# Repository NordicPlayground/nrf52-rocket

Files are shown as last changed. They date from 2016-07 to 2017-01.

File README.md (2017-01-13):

# nRF52 Rocket

# Check out the official [Launch Video](https://www.youtube.com/watch?v=nOK4TQ3TGd8) from Nordic Semiconductor!

#### Table of Contents
* [Introduction](#introduction)
* [Hardware](#hardware)
* [Firmware](#firmware)

This repository contains the firmware and hardware files for the first launched BLE rocket prototype.

## Introduction

As the BLE standard (namely Bluetooth 5.0) enables higher TX power and thusly communication range, it becomes more and more viable to use Bluetooth LE for mid-range RC toys in the proximity of around 100 - 500 m. BLE provides the benefits of high interoperability amongst different manufacturers due to rigorous standardization compared to other frequencies, yet less power consuming than Wifi.

The model rocketry industry drives a very popular hobby, especially in the U.S., that inspires youth and adults to engage in science and engineering. Yet, through some web research it appears that there is a gap between really simple beginner rockets with less than 200 m of flight range which are completely made out of cardboard and wood with no electronic flight telemetry or electronic parachute deployment; and the advanced heavy duty rockets with expensive electronics that can go up to kilometers.

A BLE enabled model rocket can serve the hobbyists who want to be a little more serious with their rocket flying and track their rockets performance in real time and have smart parachute deployment, but do not have the funds or the skills to buy/build a super hardcore rocket that costs thousands of dollars.

## Hardware

### Rocket:
#### Electronics
Componenet Type | Part Number | Function
---:|---:|---:|
Processor/RF| nRF52 | Flight Control, launch control, telemetry, communication with ground station
Radio Amplifier (PA + LNA)| Skyworks 66112-11 | Boost RF range
IMU | MPU9250 | Orientation tracking, parachute deployment upon flight peak
Pressure | MPL3115A2 | Altitude tracking based on atmospheric pressure, parachute release timing upon flight peak
Humidity/Temperature | HTU21D | Environment monitoring
Servo Motors | Tower Pro SG90 | Parachute release mechanism
5V Boost Converter  | MIC2875 | Ignition and servo power
3F Supercapacitor | PM-5R0H305-R | High current ignition reservoir
3.3V LDO | AP7333-33SAG-7 | nRF52/sensor power
USB 4.2V LiPo Charger | AAT3681A | Charging

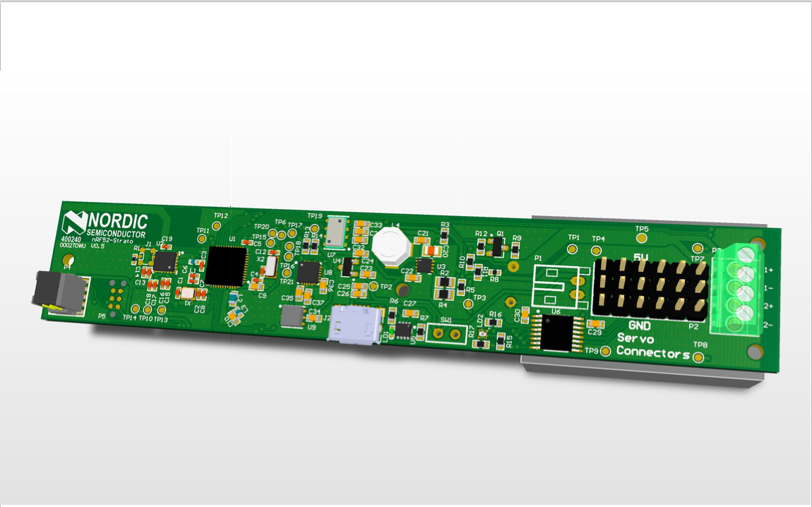
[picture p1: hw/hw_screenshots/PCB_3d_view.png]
3D View

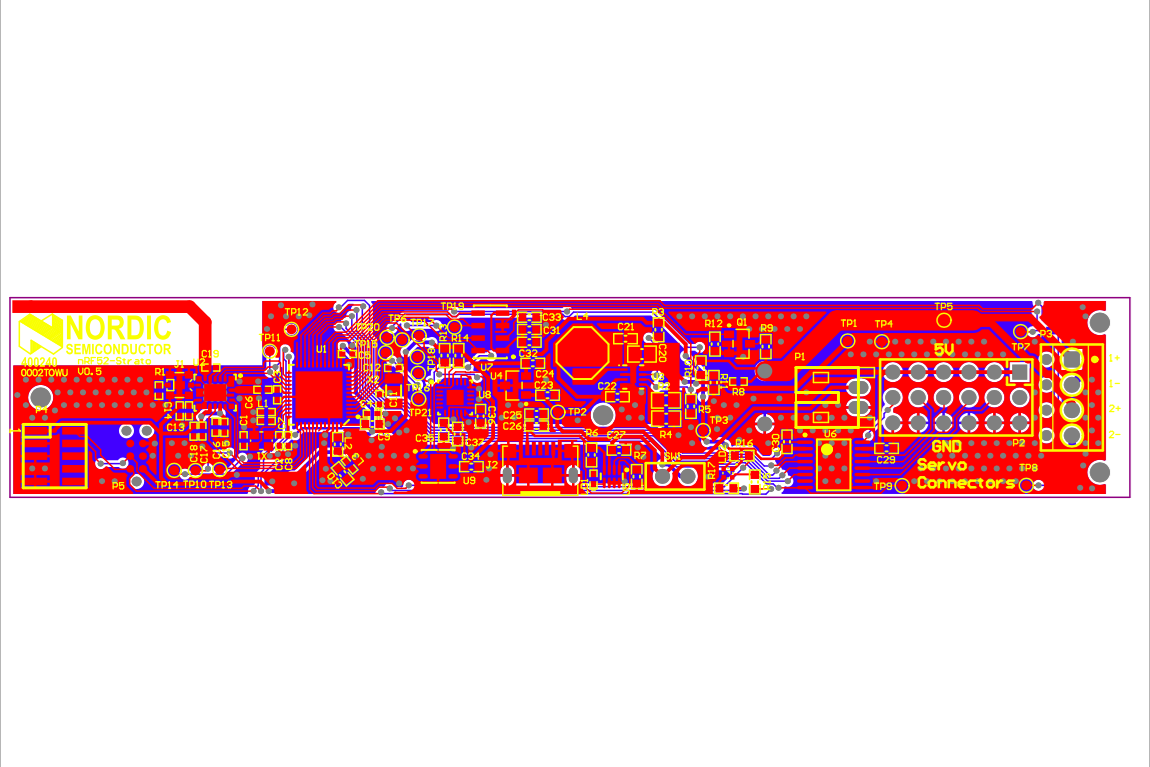
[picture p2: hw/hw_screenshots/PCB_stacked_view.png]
Stacked View


#### Mechanical
Component Type | Part Number | Function
---:|---:|---:|
Rocket Motor| Klima D9-P | Propulsion
Electronic Starters | Klima | Ignition mechanism
Parachute | Klima | Rocket recovery
Nose Cone | 3D Printed | Body construction
Engine Mount + Fins | 3D Printed | Body construction

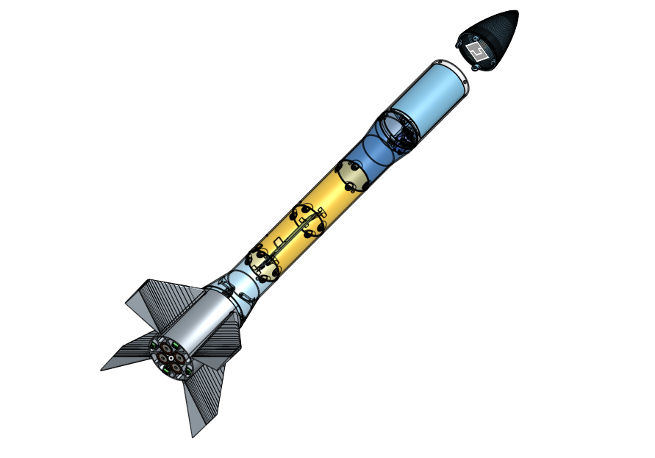
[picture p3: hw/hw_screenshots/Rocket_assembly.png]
Rocket CAD Assembly


[OnShape 3D CAD Files and Assemblies](https://cad.onshape.com/documents/a4d45ed022dbb8a2dc83f180/w/58fca6c234a131fe917f28c8/e/50b00e1e04cebf07ed807ff0 "Rocket CAD Files")

##Firmware

(Coming Soon!)

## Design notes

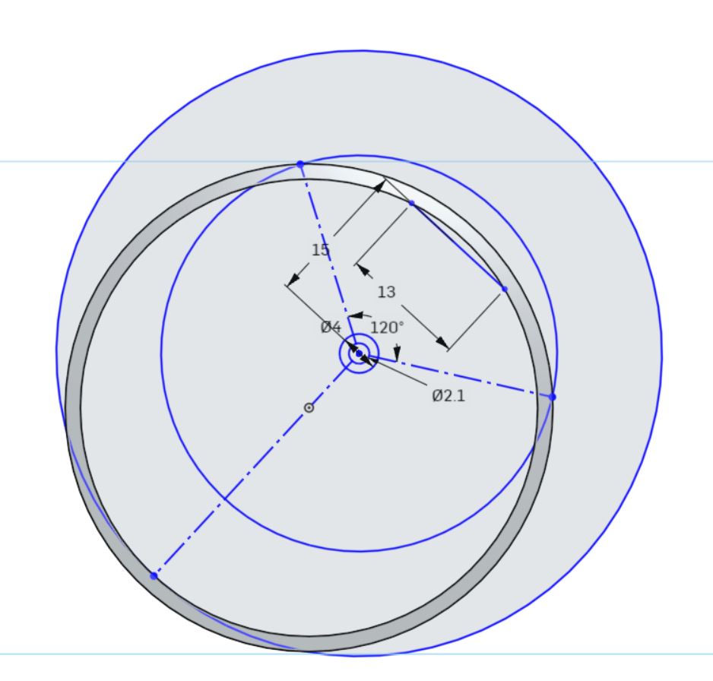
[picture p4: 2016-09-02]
hw/design process/parachute_hatch_sketch.JPG

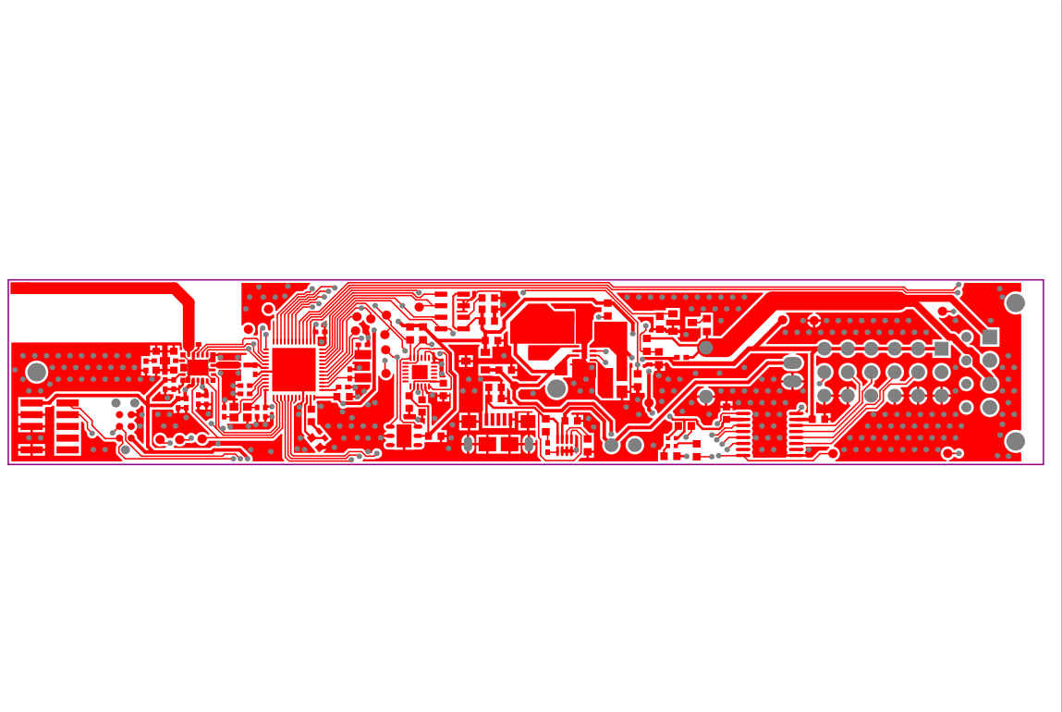
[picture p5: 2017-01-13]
hw/hw_screenshots/PCB_top_layer.png

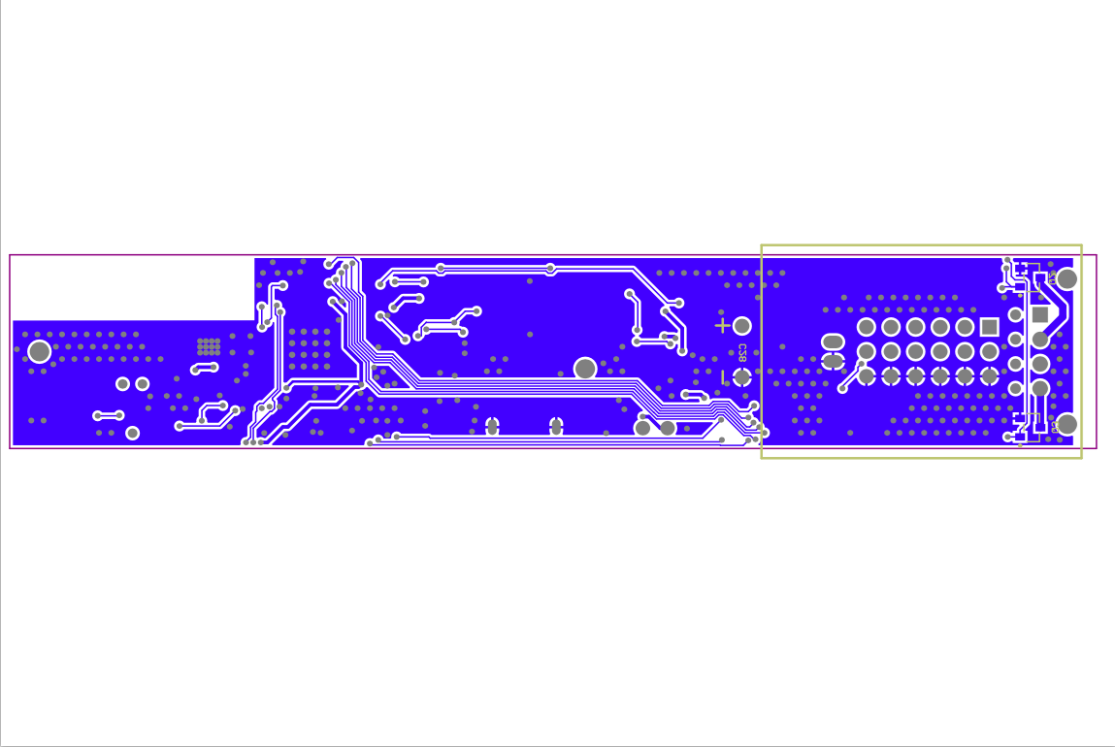
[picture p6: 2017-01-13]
hw/hw_screenshots/PCB_bottom_layer.png

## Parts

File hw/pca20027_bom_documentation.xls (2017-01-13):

Bill of material
PCB: | PCAxxxxx
Version: | <Schematic version>
Designator | Value | Description | Footprint Doc | Manufacturer | Manufacturer Part Number
C1, C2, C11, C12 | 12pF | Capacitor, NP0, ±2% | 0402
C3 | 0.8pF | Capacitor, NP0, ±5% | 0402
C4, C5, C8, C14, C16, C18, C19 | 100nF | Capacitor, X7R, ±10% | 0402
C6 | N.C. | Not mounted | 0402
C7 | 100pF | Capacitor, NP0, ±5% | 0402
C9, C21 | 4.7µF | Capacitor, X5R, ±10% | 0603
C10, C22, C23, C24 | 1.0µF | Capacitor, X7R, ±10% | 0603
C13, C15, C17 | 1.0nF | Capacitor, X7R, ±10% | 0402
C20 | 22µF | Capacitor, X5R, ±10% | 0805
C25, C27, C31 | 10µF | Capacitor, X5R, ±20% | 0603
C26, C29, C30, C32, C33, C34, C35, C37 | 100nF | Chip Cap 0603 | 0603
C28 | 3F | 3F, 5V Supercapacitor (EDLC) | PM-5R0H305-R | Cooper Industries | PM-5R0H305-R
C36 | 10nF | Chip Cap 0603 | 0603
J1 | MM8130-2600 | Coaxial Connector with Switch | COAXIAL-SWF | Murata | MM8130-2600
J2 | MicroUSB-B | MicroUSB-B-SMT | USB-Micro-B-RA-SMD-PiP | Allen Creations Corp. | AJU55-BS2111-L
L1 | 3.9nH | High frequency chip inductor ±5% | 0402 | Murata | LQP15MN3N9B02D
L2 | 10µH | Chip inductor, IDC,min = 50 mA, ±20% | 0603 | Taiyo Yuden | LBMF1608T100K
L3 | 15nH | High frequency chip inductor ±10% | 0402 | Taiyo Yuden | HK100515NJ-T
L4 | 2.2µH | FIXED IND 2.2UH 3.2A 21 MOHM SMD | SRU5028 | Bourns | SRU5028-2R2Y
LD1 | L0402G | LED, Green, 0402, Vf=2.1V, 50mcd, - 40 to +85°C | 0402 | Kingbright Company LLC | APHHS1005CGCK
LD2 | LED RGB | RGB LED 1.00 mm x 1.00 mm SMD | SML-LX0404SIUPGUSB | Lumex | SML-LX0404SIUPGUSB
P1 | HDR-2, 2mm | JST-S2B-PH-K-S (LF)(SN)-HEADER-SIDE ENTRY, 2WAY | S 2B-PH-K-S | JST | S2B-PH-K-S (LF)(SN)
P2 | Pin Header 3x6 | Pin Header 3x6, 2.54mm (100mil) | HDR_3x6
P3 | Conn-4 | PHOENIX CONTACT - 1725672 - TERMINAL BLOCK, PCB, 2.54MM, 4WAY | MPT 0,5/4-2,54 | Phoenix | 1725672
P4 | Pin Header 2x5, 1.27mm, SWD | Pin Header 2x5, 1.27mm (50mil), SMD, Keying Shroud, Removed Pin 7 | HDR_2x5-SMD-1.27mm-SWD | Samtec | FTSH-105-01-F-DV-K
Q1 | FDV303N | Mosfet FDV303N | SOT-23a
Q2, Q3 | Si2342DS | N-Channel 8V MOSFET | SOT-23a | Vishay Siliconix | Si2342DS
R1 | 50R | Resistor, ±1%, 0.063W | 0402
R2 | 910k | Resistor, ±0.1%, 0.125W | 0805 | Panasonic | ERA-6AEB914V
R3, R10, R11 | 1M0 | Resistor, ±1%, 0.06W | 0603
R4 | 200k | Resistor, ±0.1%, 0.125W | 0805 | Panasonic | ERA-6AEB204V
R5 | 10k | Resistor, ±1%, 0.1W | 0603
R6 | 1k2 | Resistor, ±1%, 0.06W | 0603
R7 | 8k2 | Resistor, ±1%, 0.06W | 0603
R8 | 5R6 | Resistor, ±1%, 0.063W | 0402
R9 | 1k | Resistor, ±1%, 0.06W | 0603
R12 | 100k | Resistor, ±1%, 0.06W | 0603
R13, R14 | 4k7 | Resistor, ±1%, 0.06W | 0603
R15 | 2k2 | Resistor, ±1%, 0.06W | 0603
R16 | 680R | Resistor, ±1%, 0.06W | 0603
R17 | 820R | Resistor, ±1%, 0.06W | 0603
SW1 | SW-SPST | Slide Switch SPST 125V, 500mA DC, 11A AC | GF-1123-0009 | CW Industries | GF-1123-0009
U1 | nRF52832-QFAA | Multi-protocol Bluetooth Low Energy and 2.4GHz proprietary system-on-chip | QFN-48 | Nordic Semiconductor | nRF52832-QFAA
U2 | SKY66112-11 | 2.4 GHz ZigBee®/Thread/Bluetooth® Smart Front-End Module | SKY66112-11 | Skyworks | SKY66112-11
U3
U4 | AP7333-33SAG-7 | 300mA, Low Quiescent Current, Fast Transient Low Dropout Linear Regulator | SOT-23-3 | Diodes Incorporated | AP7333-33SAG-7
U5 | AAT3681A | 500mA USB Port or AC Adapter Li-Ion/Polymer Battery Charger | TFSOJ-8 | Skyworks | AAT3681AIJS-4.2-T1
U6 | TXB0106 | 6-bit bidirectional voltage-level translator with auto-direction sensing | TSSOP-16 | Texas Instruments | TXB0106PWR
U7 | MPL3115A2 | MEMS accurate Pressure/Altitude and Temperature sensor with I2C interface | LGA-8 | Freescale | MPL3115A2
U8 | MPU-9250 | 9-axis MotionTracking™ Device | QFN-24 | InvenSense | MPU-9250
U9 | HTU21D | I2C Digital Relative Humidity sensor with Temperature output | DFN-6 | Measurement Specialties | HTU21D
X1 | 32MHz | XTAL SMD 2016, 32MHz, Cl=8pF, Total Tol: ±40ppm | XTAL_2016 | Epson Toyocom | Q22FA12800025
X2 | 32.768kHz | XTAL SMD 3215, 32.768kHz, 9pF, ±20ppm | XTAL_3215 | Epson Toyocom | FC-135 32.768KHZ ±20PPM,9.0PF

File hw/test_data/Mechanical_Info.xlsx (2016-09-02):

Component | Qty | Unit Mass (g) | Mass (g)
Parachute 55cm | 1 | 10 | 10
D9-P Motors | 2 | 26.5 | 53
Servo | 5 | 9 | 45
Parachute Hatch | 1 | 63 | 63
3F Supercapacitor | 1 | 7.8 | 7.8
800 mAh LiPo | 1 |  | 0
Total Mass |  |  | 178.8
Thruster Mass
Component | Qty | Unit Mass (g) | Mass (g)
D9-P Motors | 2 | 26.5 | 53
Servo | 4 | 9 | 36
Printed Thruster | 1 | 71 | 71
Total Mass |  |  | 160

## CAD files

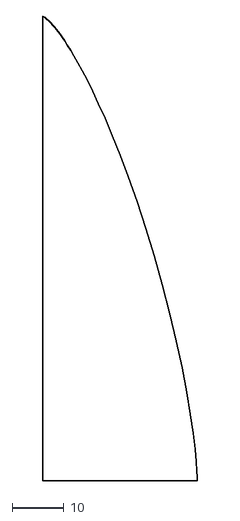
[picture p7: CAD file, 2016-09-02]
hw/3d_models/imported_models/haack-nosecone.dxf
30.0 x 90.0

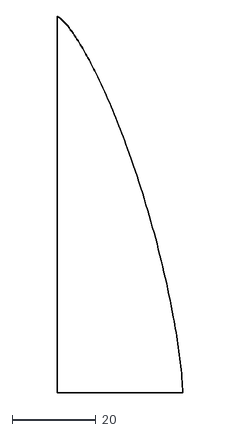
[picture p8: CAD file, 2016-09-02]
hw/3d_models/imported_models/haack-nosecone-200.dxf
30.0 x 90.0

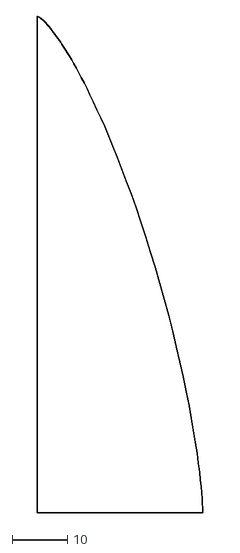
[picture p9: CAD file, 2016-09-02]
hw/3d_models/imported_models/haack-nosecone-500.dxf
30.0 x 90.0

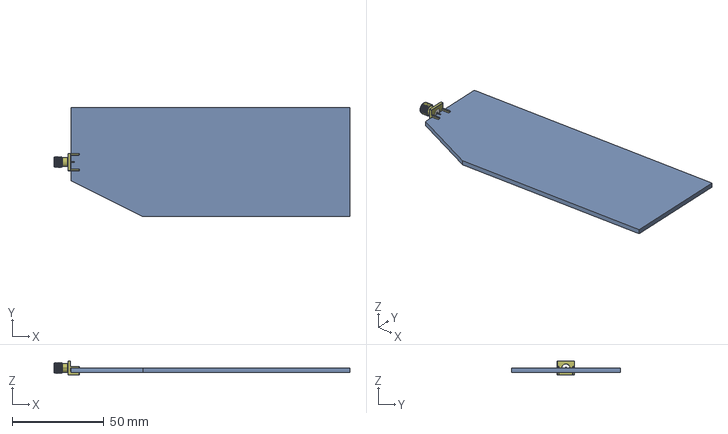
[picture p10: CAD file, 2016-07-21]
hw/3d_models/imported_models/fin_v021_sma.step
161.8 x 59.8 x 7.92 mm
Board
User_Library-SMA_PCB_EDGE_142-0701-851

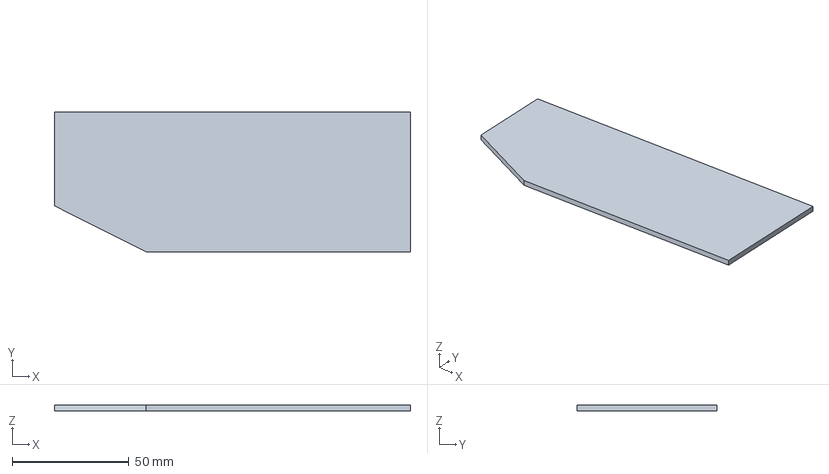
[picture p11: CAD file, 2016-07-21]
hw/3d_models/imported_models/fin_v021.step
152.4 x 59.8 x 2.40 mm

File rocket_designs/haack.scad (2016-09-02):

// Length of cone
L = 90;
// Radius of cone at base
R = 30;
// Haack coefficient. LD-Haack (Von Kármán): 0, LV-Haack = .3333
C = 0;
// Number of longitudinal faces to calculate.
num_faces = 500;
// Number of radial faces for the rotate extrude.
$fn = 300;



function theta(x) = acos(1 - 2*x/L);
function y(x) = R * sqrt(theta(x)*PI/180 - sin(2*theta(x))/2 + C * pow(sin(theta(x)), 3)) / sqrt(PI);

pts = concat([[0, 0]], [ for (i = [0 : num_faces]) let (x = i * L / num_faces) [y(L - x), x] ]);

polygon(points = pts);

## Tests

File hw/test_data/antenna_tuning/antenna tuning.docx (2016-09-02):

nRF52-Strato Antenna Tuning

0.8 pF

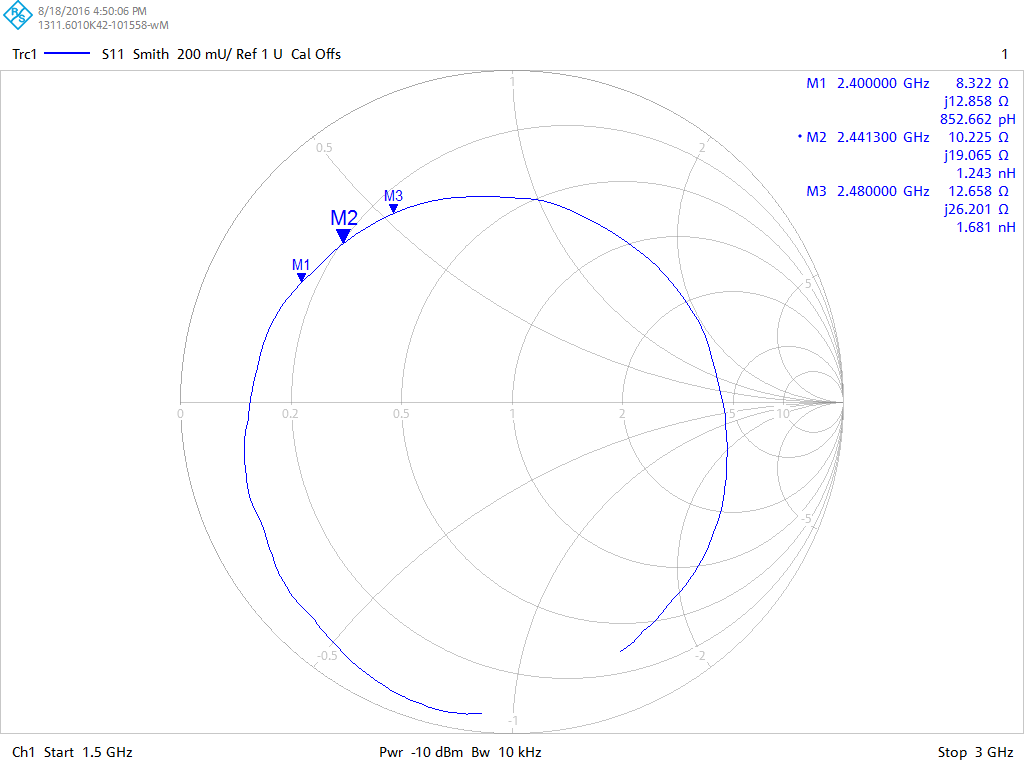
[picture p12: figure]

1.8 pF

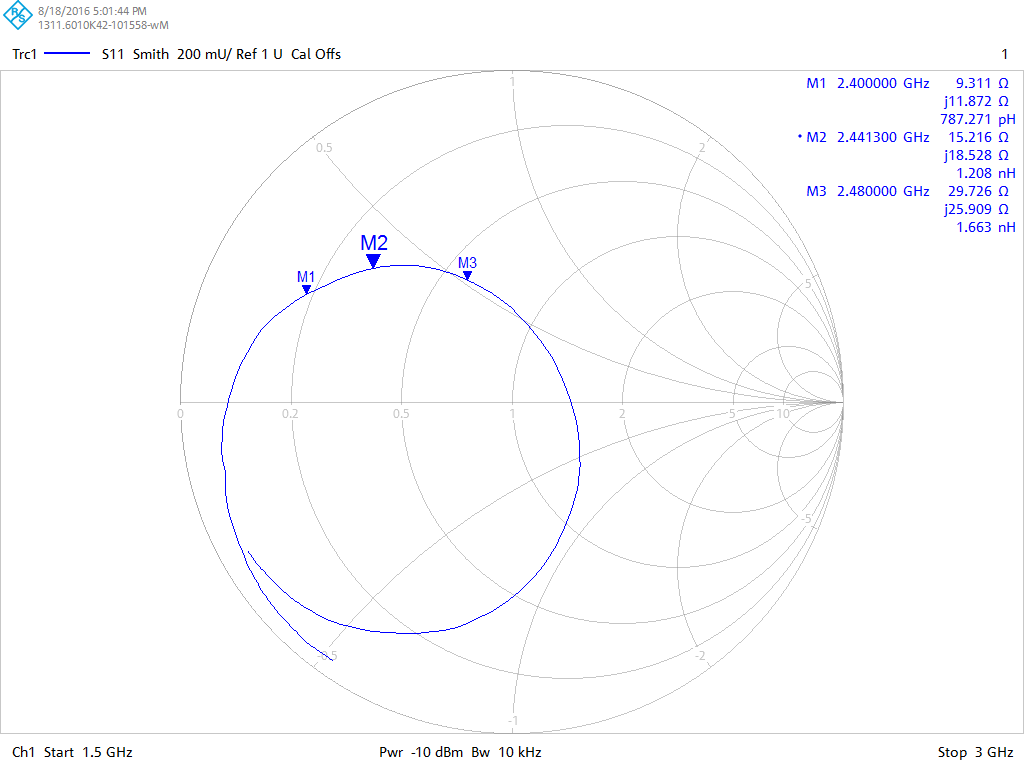
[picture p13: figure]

1.8 pF trim 1

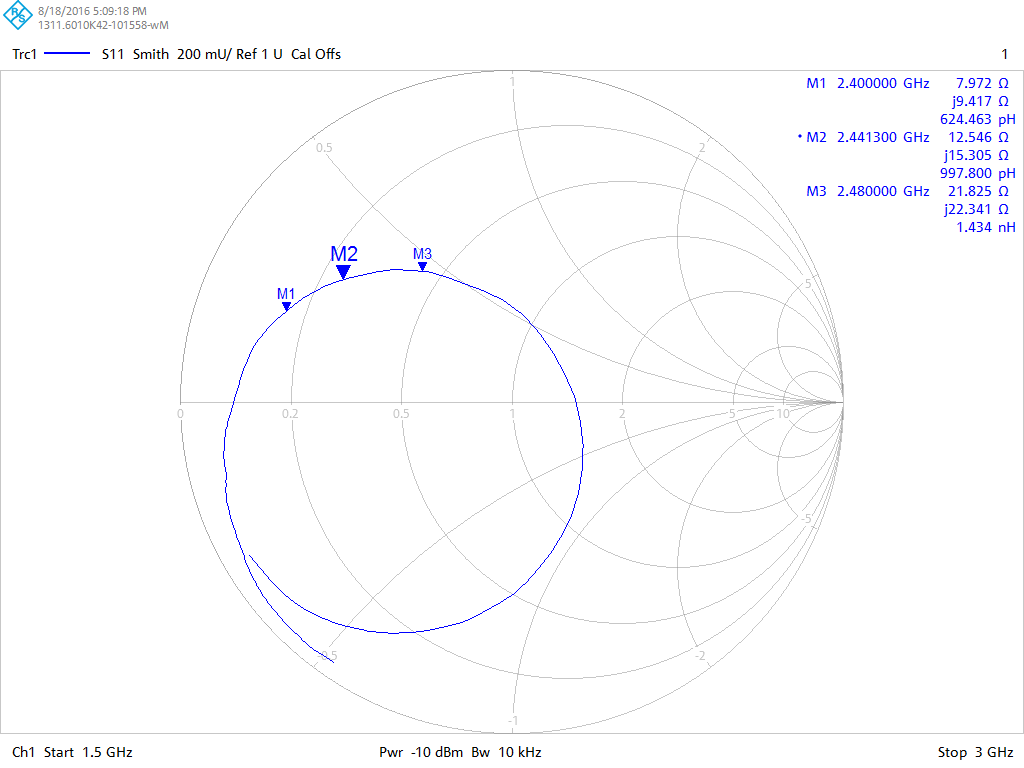
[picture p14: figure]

1.8 pF trim 2

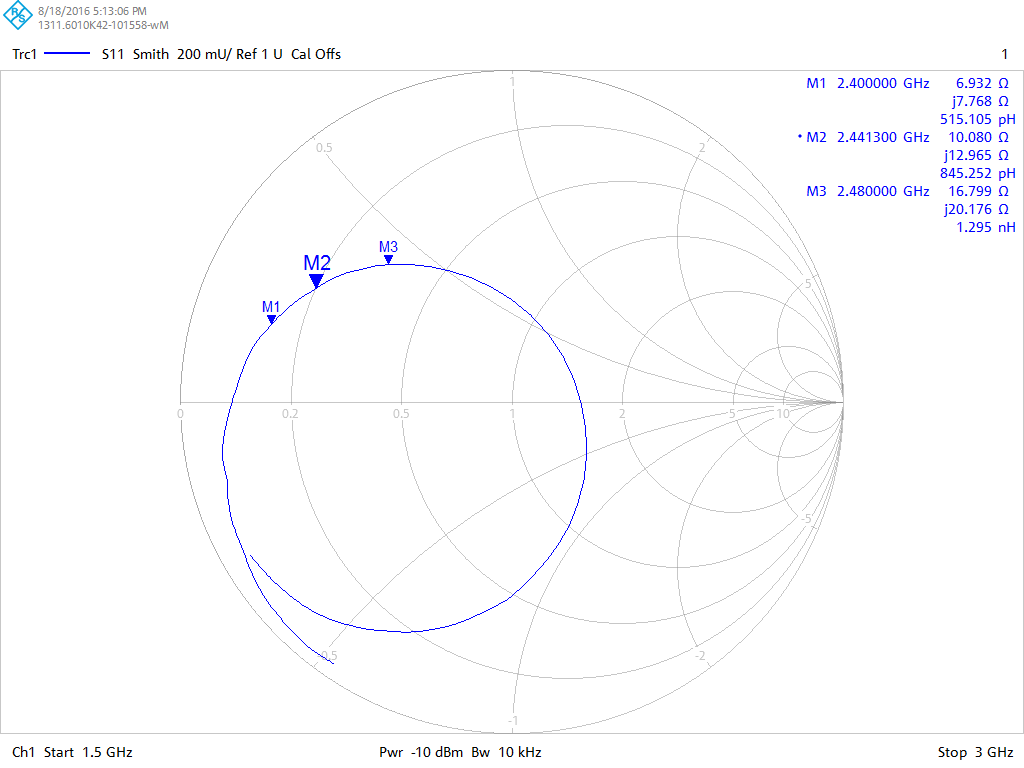
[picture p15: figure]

No capacitor trim 2

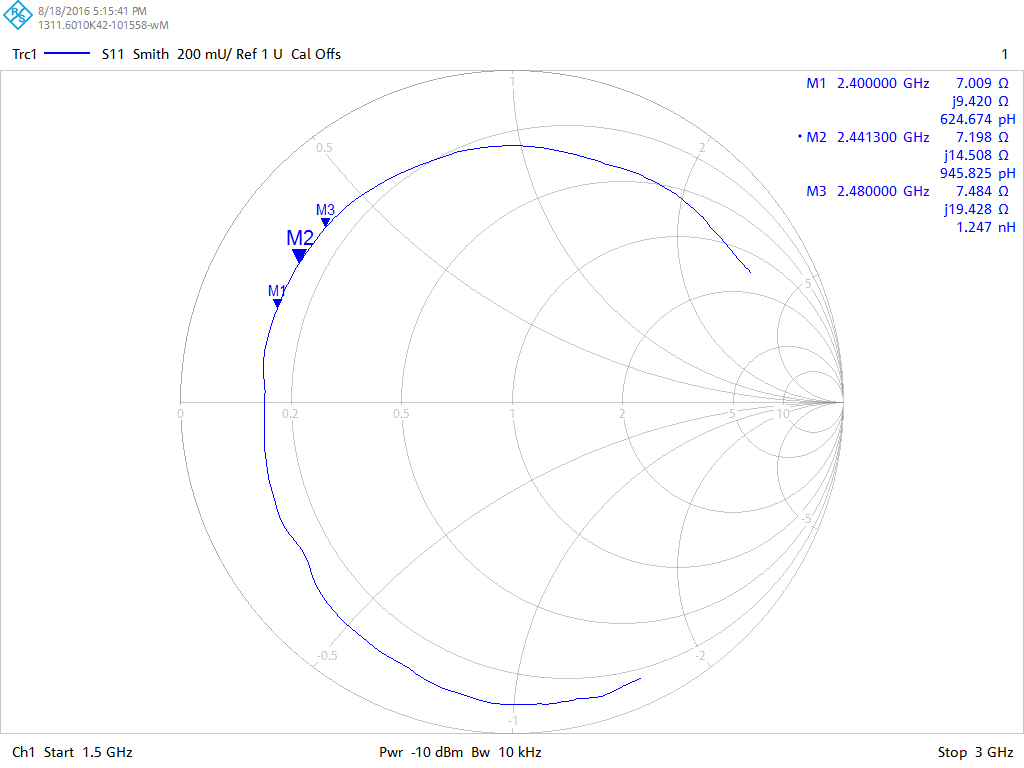
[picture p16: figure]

No cap trim 3

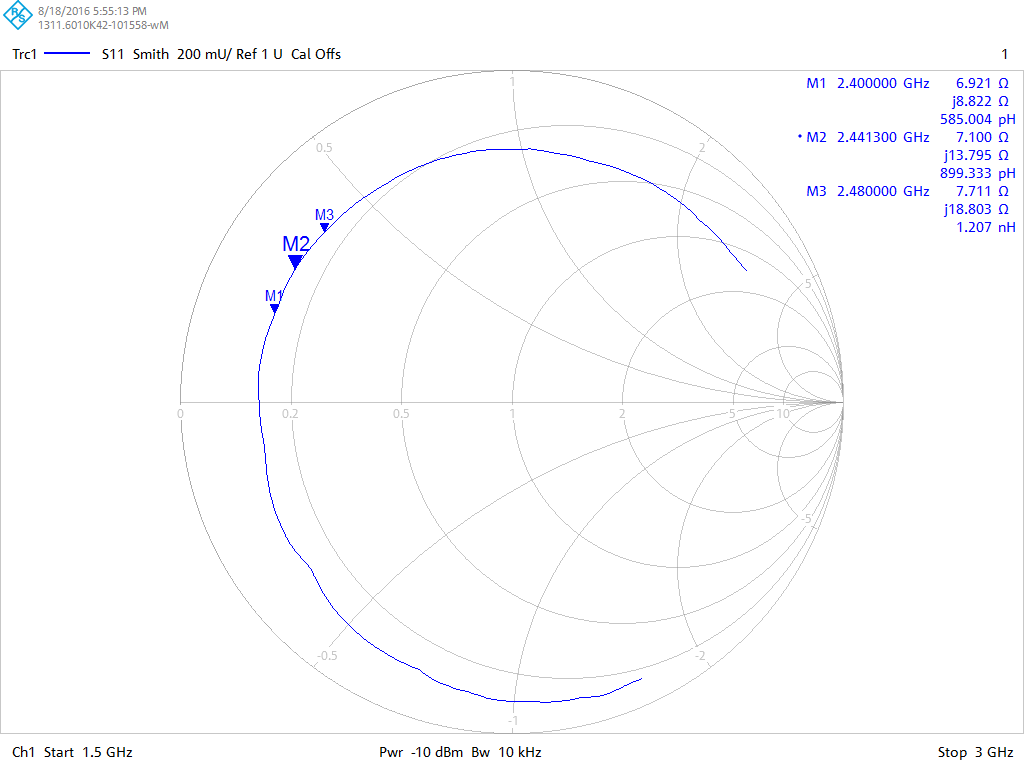
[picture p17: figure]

2.4 pF trim 2

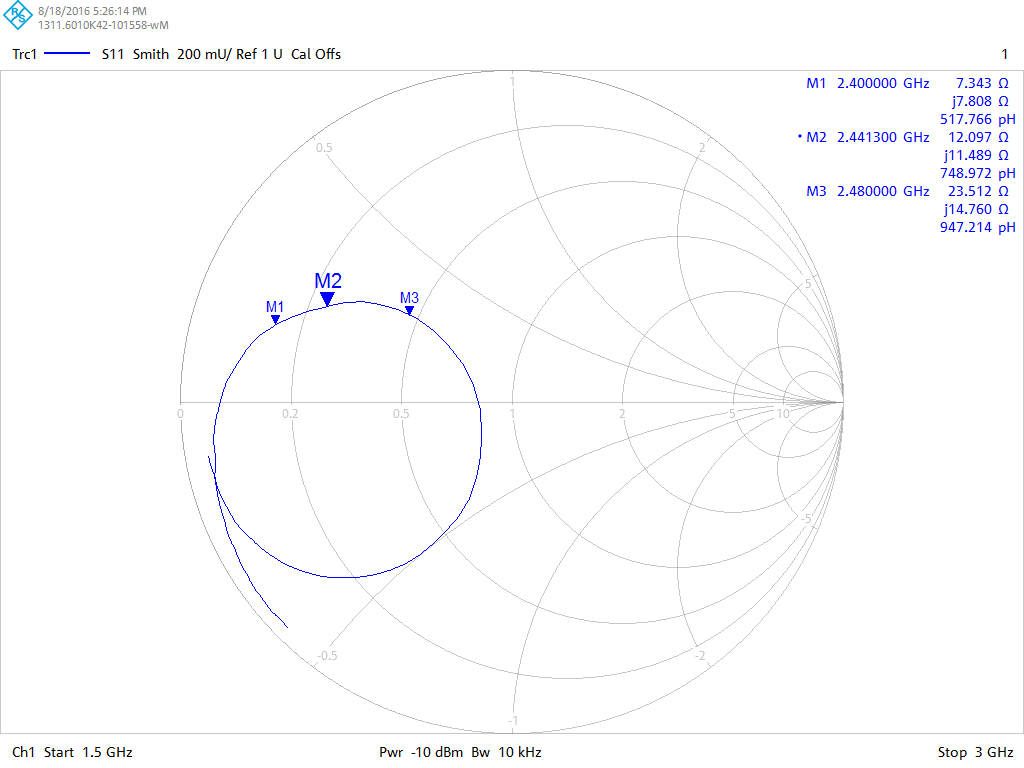
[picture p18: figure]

5.6 pF trim 2

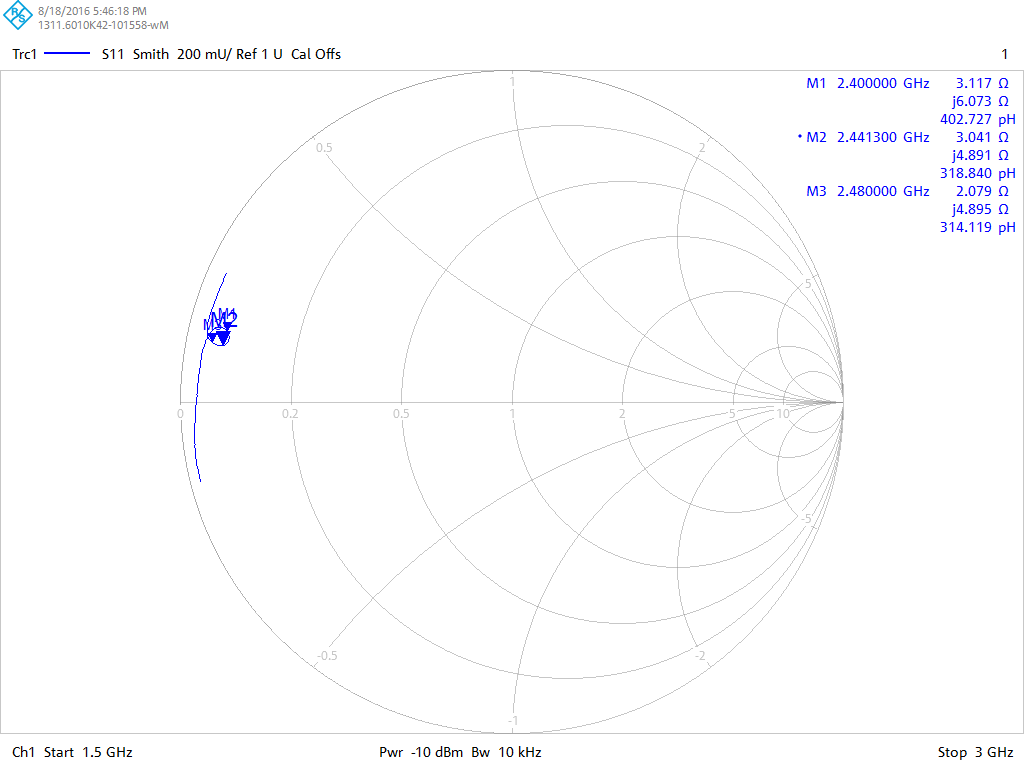
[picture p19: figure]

0.3 pF trim 3

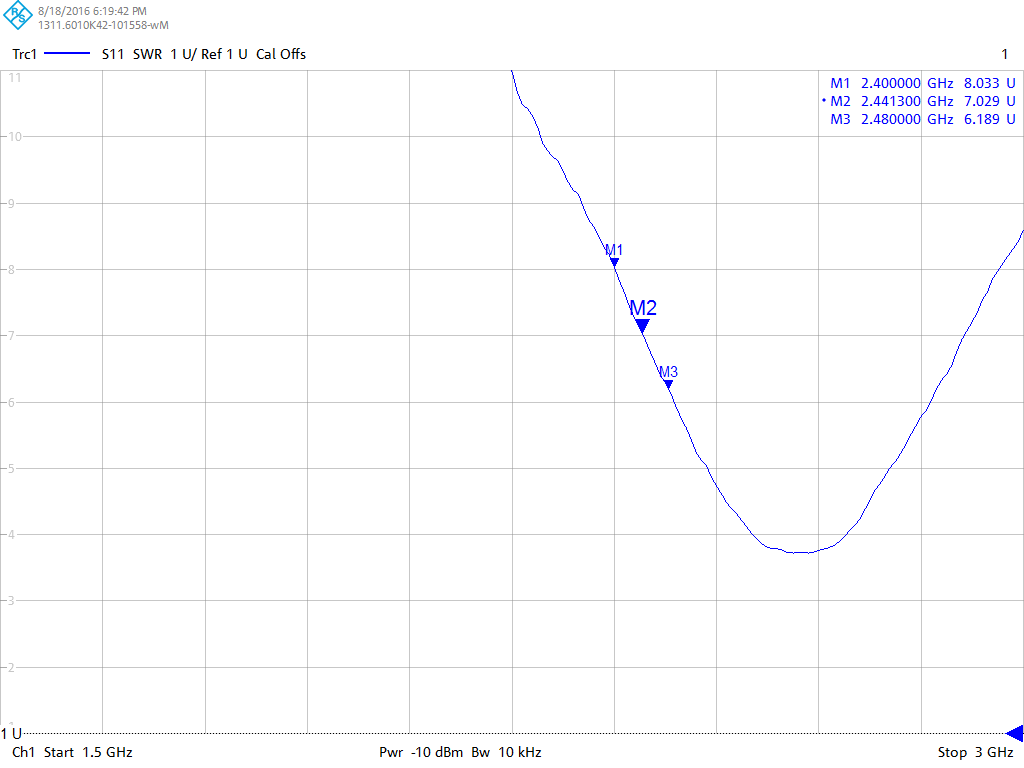
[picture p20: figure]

Extended with copper tape, 0.3 pF

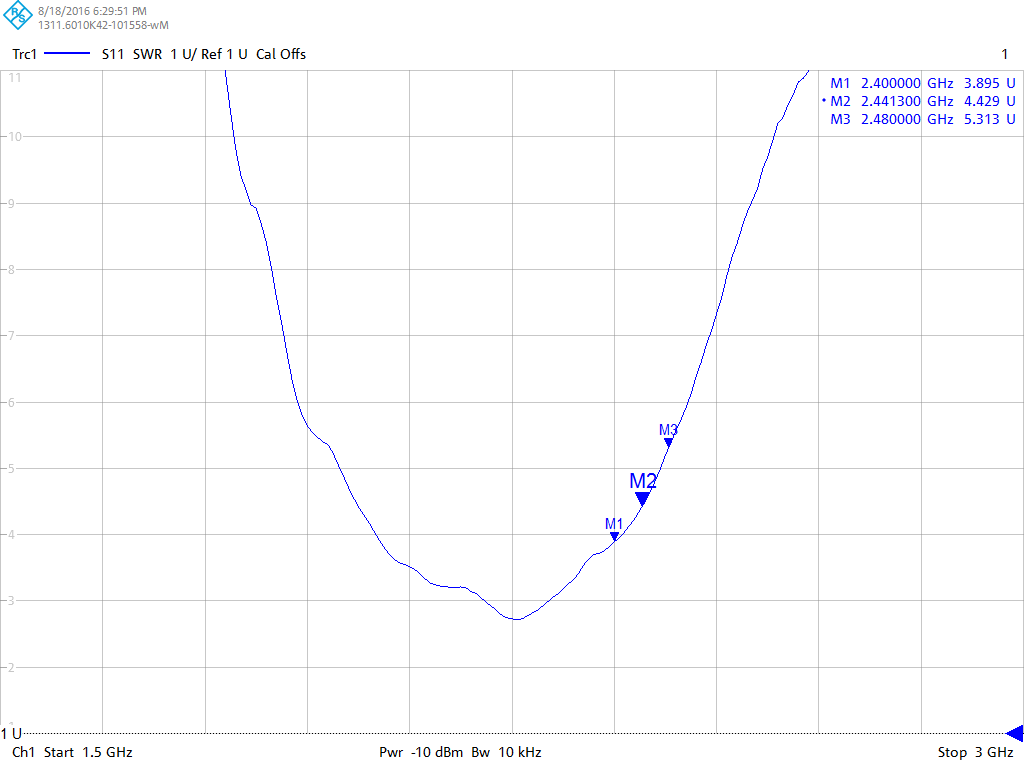
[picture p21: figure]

Extended with copper tape trim 1, 1pF


Extended with copper tape trim 1, 1.5 pF


Extended with copper tape trim 2, 1.5 pF


Extended with copper tape trim 3, 1.5 pF


Extended with copper tape trim 4, 1.5 pF


Extended with copper tape trim 5, 1.8 pF


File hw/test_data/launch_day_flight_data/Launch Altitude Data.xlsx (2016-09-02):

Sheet: Drone Flight
Column 0 | Column1 | Column2 | Column3 | Column4 | height | max height | speed | max speed
0 | 1 | 1 | 1 | 1 | 1 | 1 | 1 | 1
1 | 0 | 1 | FFFF | 1 | 0 | 1 | -1 | 1
2 | 0 | 1 | 0 | 1 | 0 | 1 | 0 | 1
3 | 0 | 1 | 0 | 1 | 0 | 1 | 0 | 1
4 | 0 | 1 | 0 | 1 | 0 | 1 | 0 | 1
5 | 1 | 1 | 1 | 1 | 1 | 1 | 1 | 1
6 | 1 | 1 | 0 | 1 | 1 | 1 | 0 | 1
7 | 0 | 1 | FFFF | 1 | 0 | 1 | -1 | 1
8 | 0 | 1 | 0 | 1 | 0 | 1 | 0 | 1
9 | 0 | 1 | 0 | 1 | 0 | 1 | 0 | 1
10 | 1 | 1 | 1 | 1 | 1 | 1 | 1 | 1
11 | 1 | 1 | 0 | 1 | 1 | 1 | 0 | 1
12 | 1 | 1 | 0 | 1 | 1 | 1 | 0 | 1
13 | 1 | 1 | 0 | 1 | 1 | 1 | 0 | 1
14 | 0 | 1 | FFFF | 1 | 0 | 1 | -1 | 1
15 | 0 | 1 | 0 | 1 | 0 | 1 | 0 | 1
16 | 1 | 1 | 1 | 1 | 1 | 1 | 1 | 1
17 | 0 | 1 | FFFF | 1 | 0 | 1 | -1 | 1
18 | 0 | 1 | 0 | 1 | 0 | 1 | 0 | 1
19 | 0 | 1 | 0 | 1 | 0 | 1 | 0 | 1
20 | 0 | 1 | 0 | 1 | 0 | 1 | 0 | 1
21 | 0 | 1 | 0 | 1 | 0 | 1 | 0 | 1
22 | 0 | 1 | 0 | 1 | 0 | 1 | 0 | 1
23 | 1 | 1 | 1 | 1 | 1 | 1 | 1 | 1
24 | 0 | 1 | FFFF | 1 | 0 | 1 | -1 | 1
25 | 1 | 1 | 1 | 1 | 1 | 1 | 1 | 1
26 | 1 | 1 | 0 | 1 | 1 | 1 | 0 | 1
27 | 0 | 1 | FFFF | 1 | 0 | 1 | -1 | 1
28 | 1 | 1 | 1 | 1 | 1 | 1 | 1 | 1
29 | 1 | 1 | 0 | 1 | 1 | 1 | 0 | 1
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

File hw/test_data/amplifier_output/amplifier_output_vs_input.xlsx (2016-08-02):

IN (dBm) | Gain (dB) | OUT (dBm)
4 | 16.56 | 20.56
3 | 17.73 | 20.73
0 | 20.25 | 20.25
-4 | 22.16 | 18.16
-8 | 19.05 | 11.05
-12 | 15.81 | 3.81
-16 | 14.12 | -1.88
-20 | 13.32 | -6.68
-30 | 12.86 | -17.14
-40 | 12.75 | -27.25

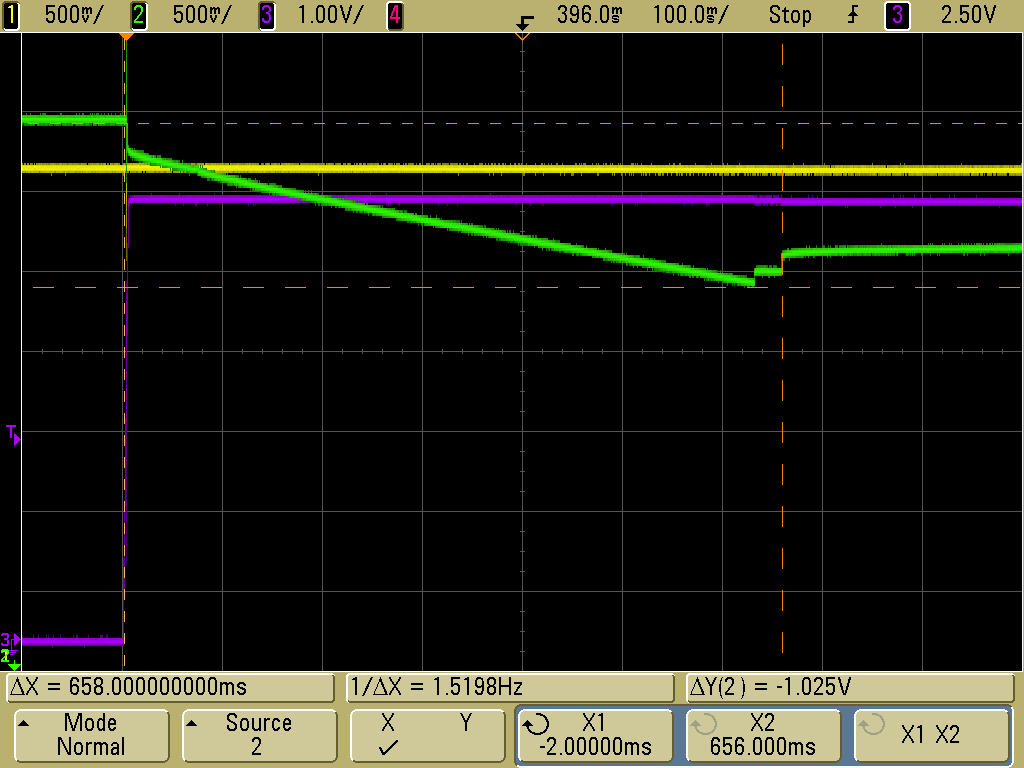
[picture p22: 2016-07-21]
hw/test_data/ignition_tests/2_igniters_in_parallel/via supercap, pre-smoked igniters.png

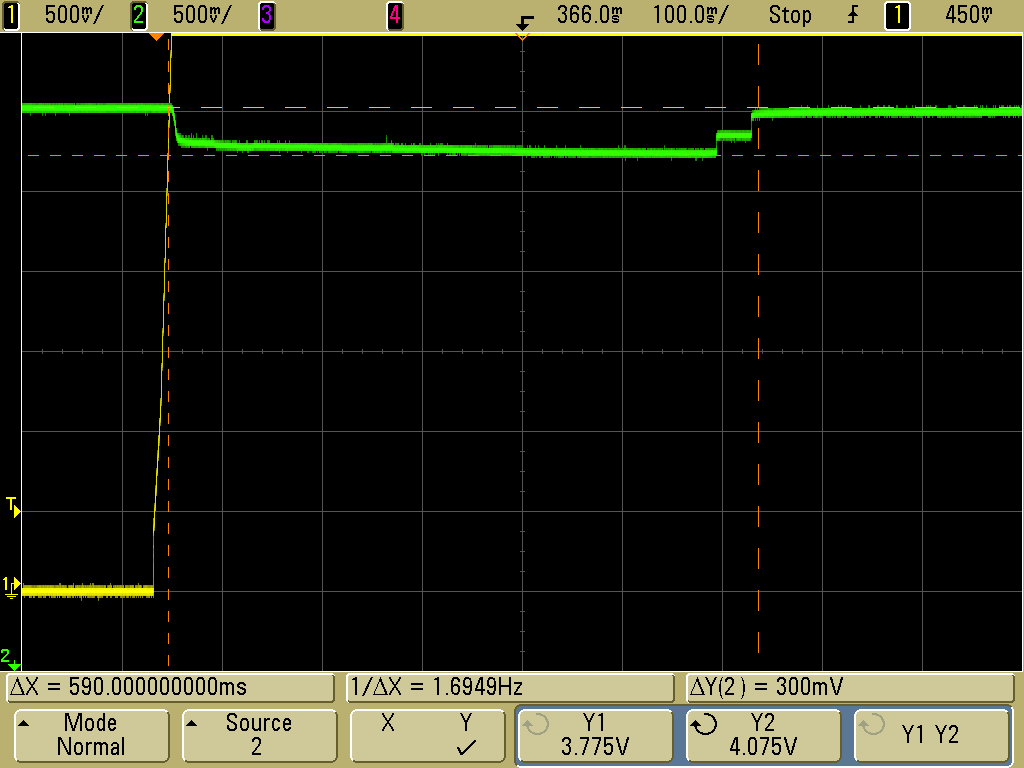
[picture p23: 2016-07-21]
hw/test_data/ignition_tests/2_igniters_in_parallel/via battery.png

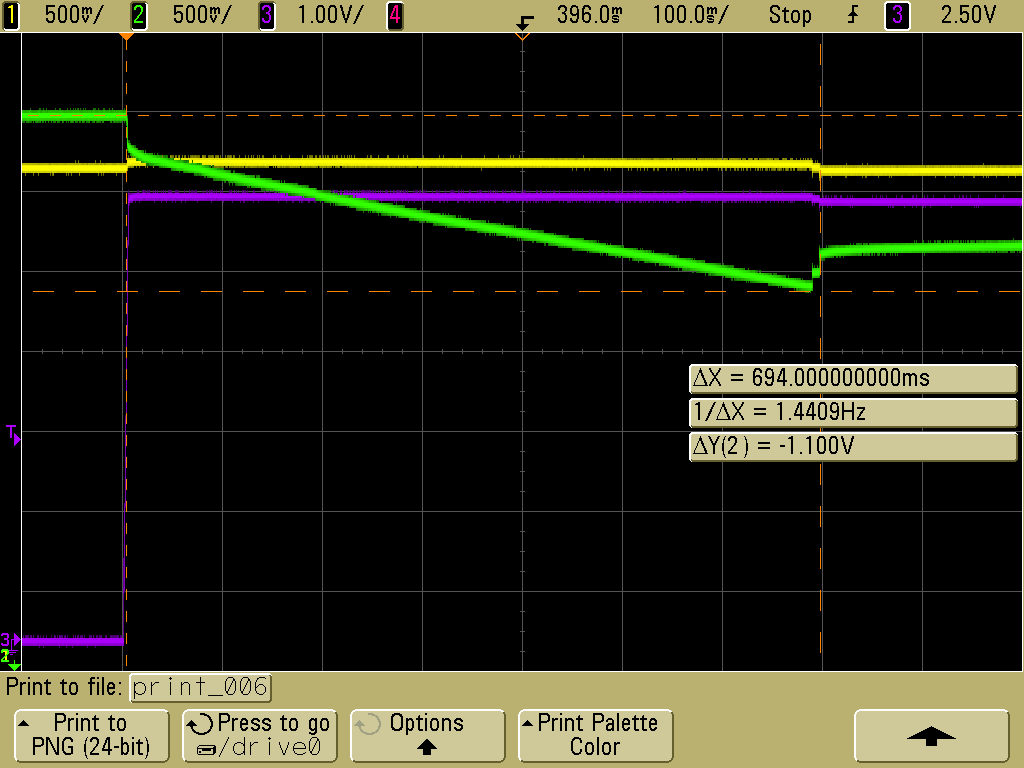
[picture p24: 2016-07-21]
hw/test_data/ignition_tests/2_igniters_in_parallel/via supercap, fresh igniters.png

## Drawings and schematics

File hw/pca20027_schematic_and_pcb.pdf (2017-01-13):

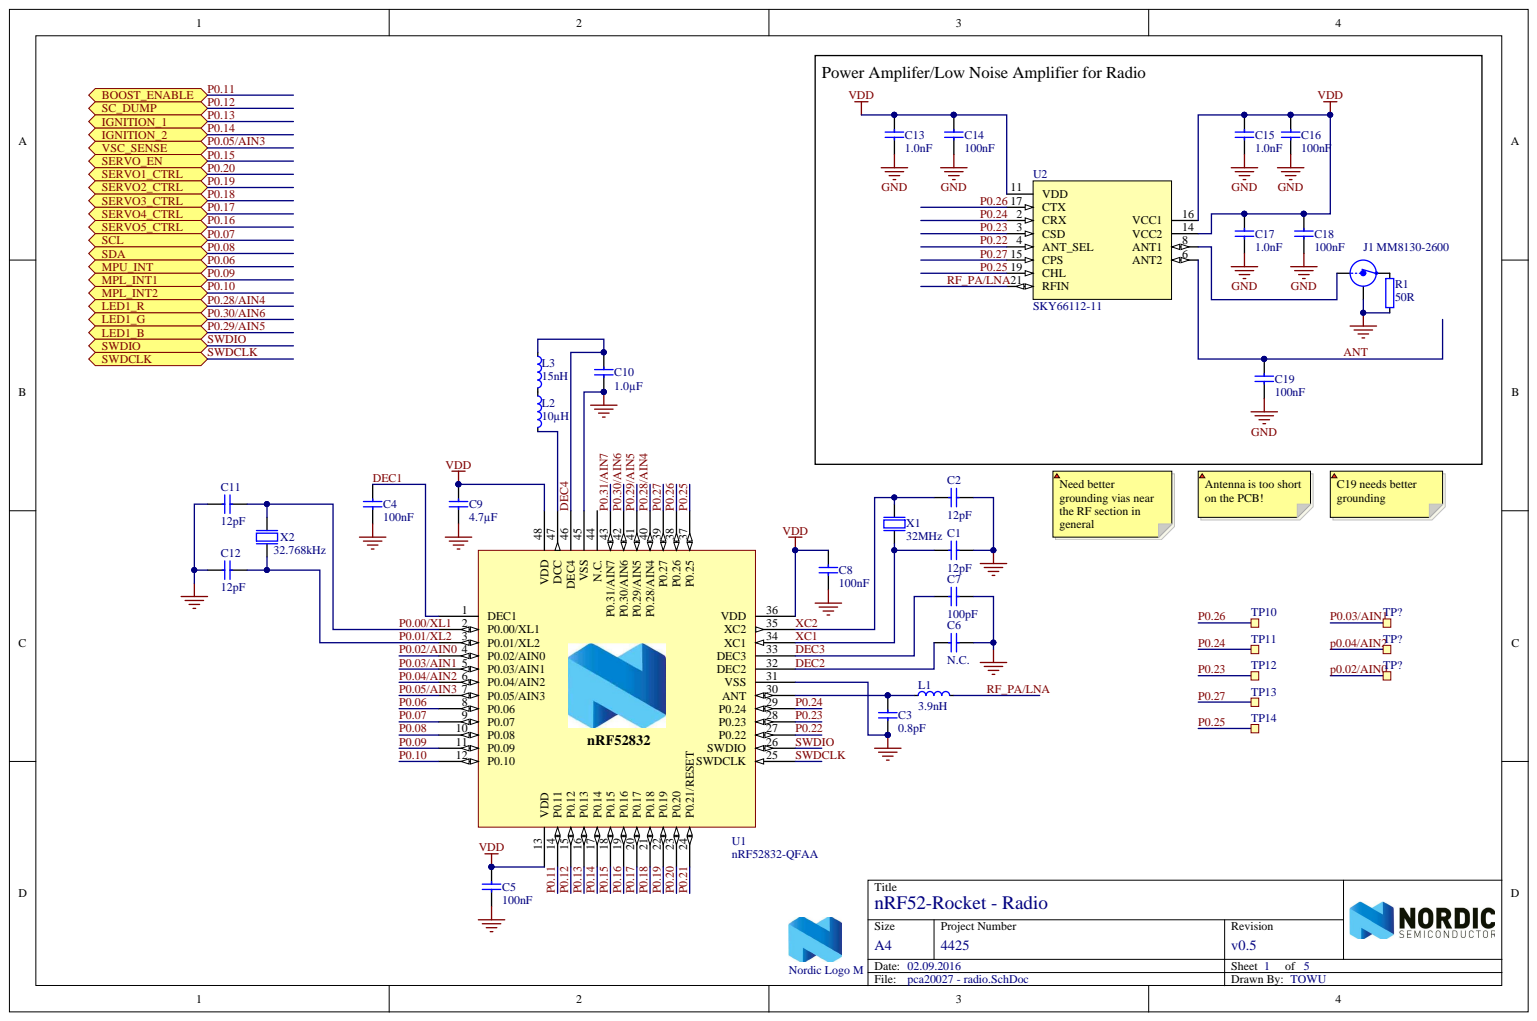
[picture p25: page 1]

Power Amplifer/Low Noise Amplifier for Radio

GND | ANT

Need better
grounding vias near
the RF section in
general

Antenna is too short
on the PCB!

Title nRF52-Rocket - Radio

Size A4 | Project Number 4425 | Revision v0.5

Date: 02.09.2016 | Sheet of
File: pca20027 - radio.SchDoc | Drawn By: TOWU

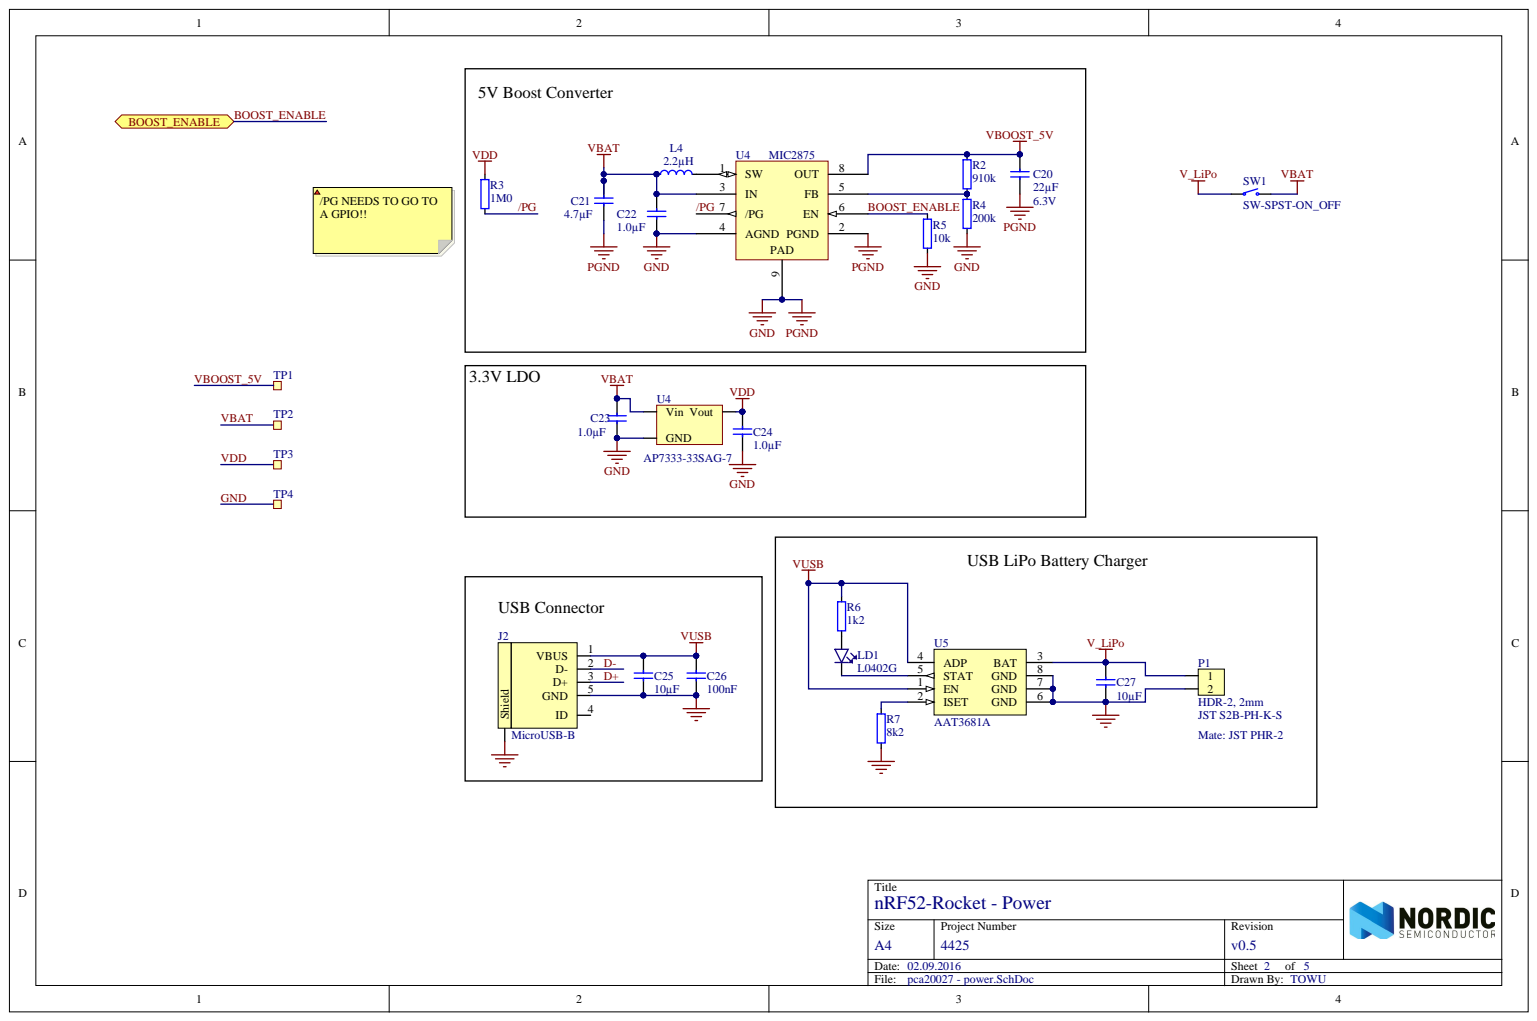
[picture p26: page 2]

/PG NEEDS TO GO TO
A GPIO!!

USB LiPo Battery Charger

Title nRF52-Rocket - Power

Size A4 | Project Number 4425 | Revision v0.5

pca20027 - power.SchDoc

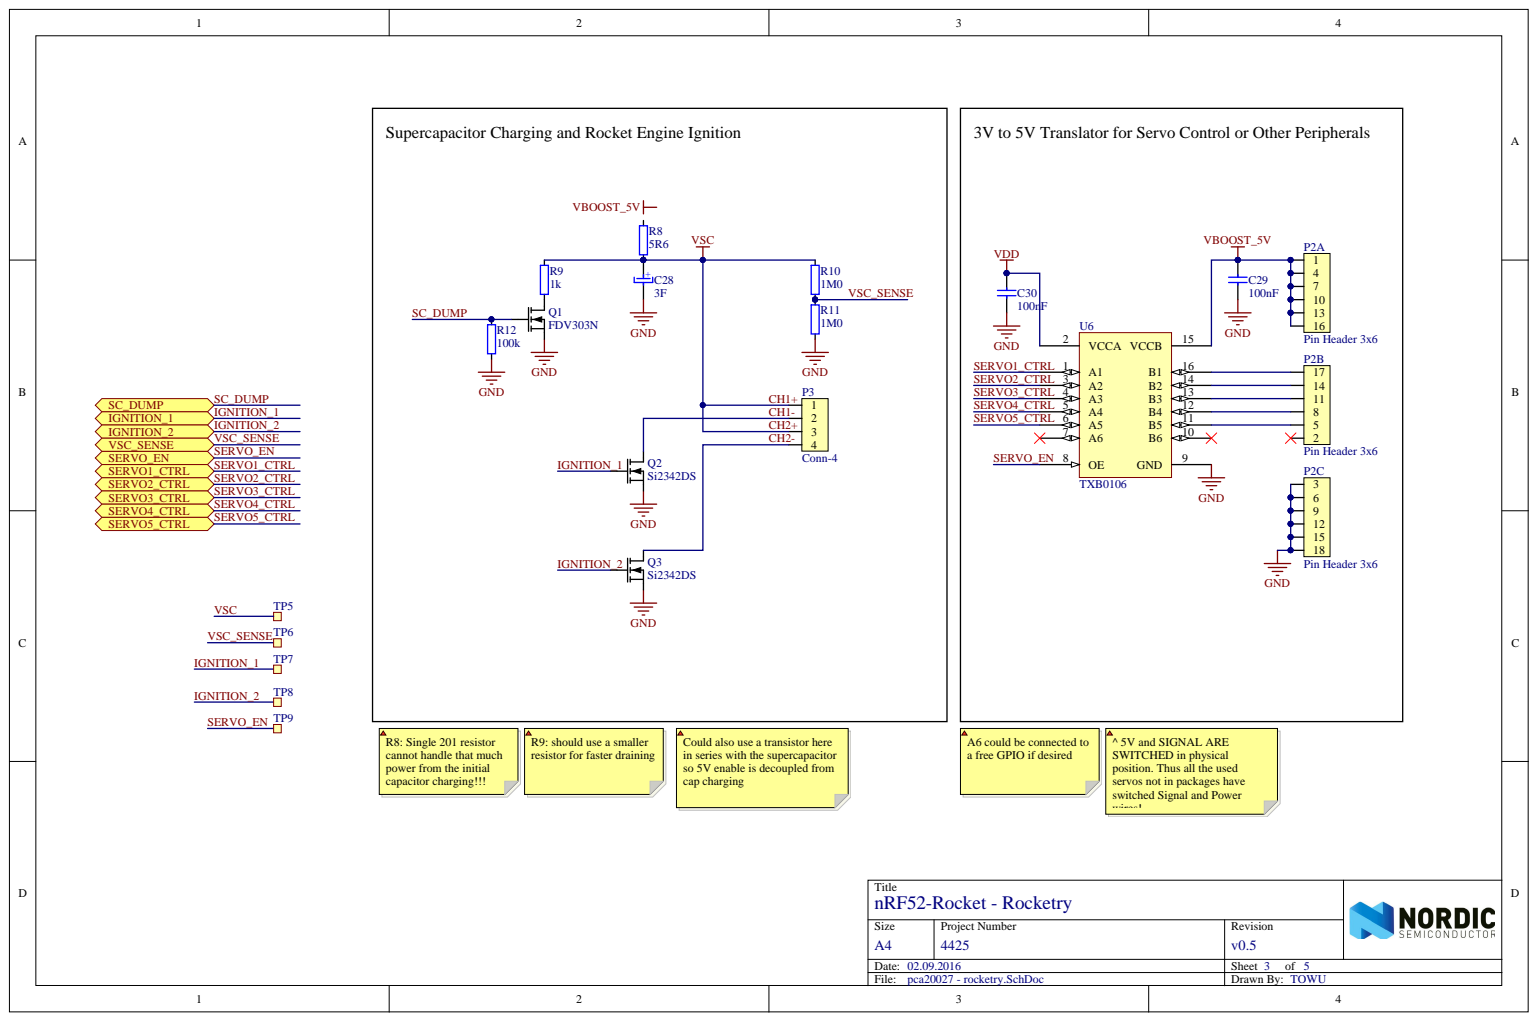
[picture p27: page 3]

CH1-
CH2+

R8: Single 201 resistor
cannot handle that much
power from the initial
capacitor charging!!!

R9: should use a smaller
resistor for faster draining

Could also use a transistor here
in series with the supercapacitor
so 5V enable is decoupled from
cap charging

A6 could be connected to
a free GPIO if desired

^ 5V and SIGNAL ARE
SWITCHED in physical
position. Thus all the used
servos not in packages have
switched Signal and Power
wires!

Title nRF52-Rocket - Rocketry

Size A4 | Project Number 4425 | Revision v0.5

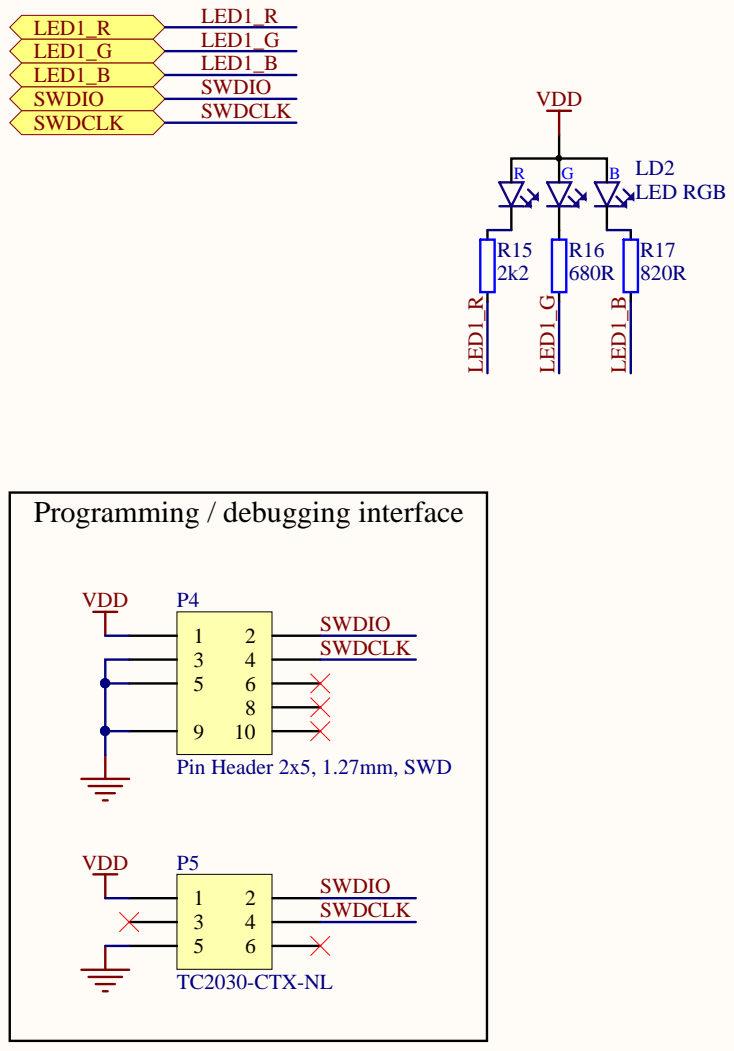
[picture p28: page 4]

Title nRF52-Rocket - User Interface

Size A4 | Project Number 4425 | Revision v0.5

pca20027 - user_interface.SchDoc

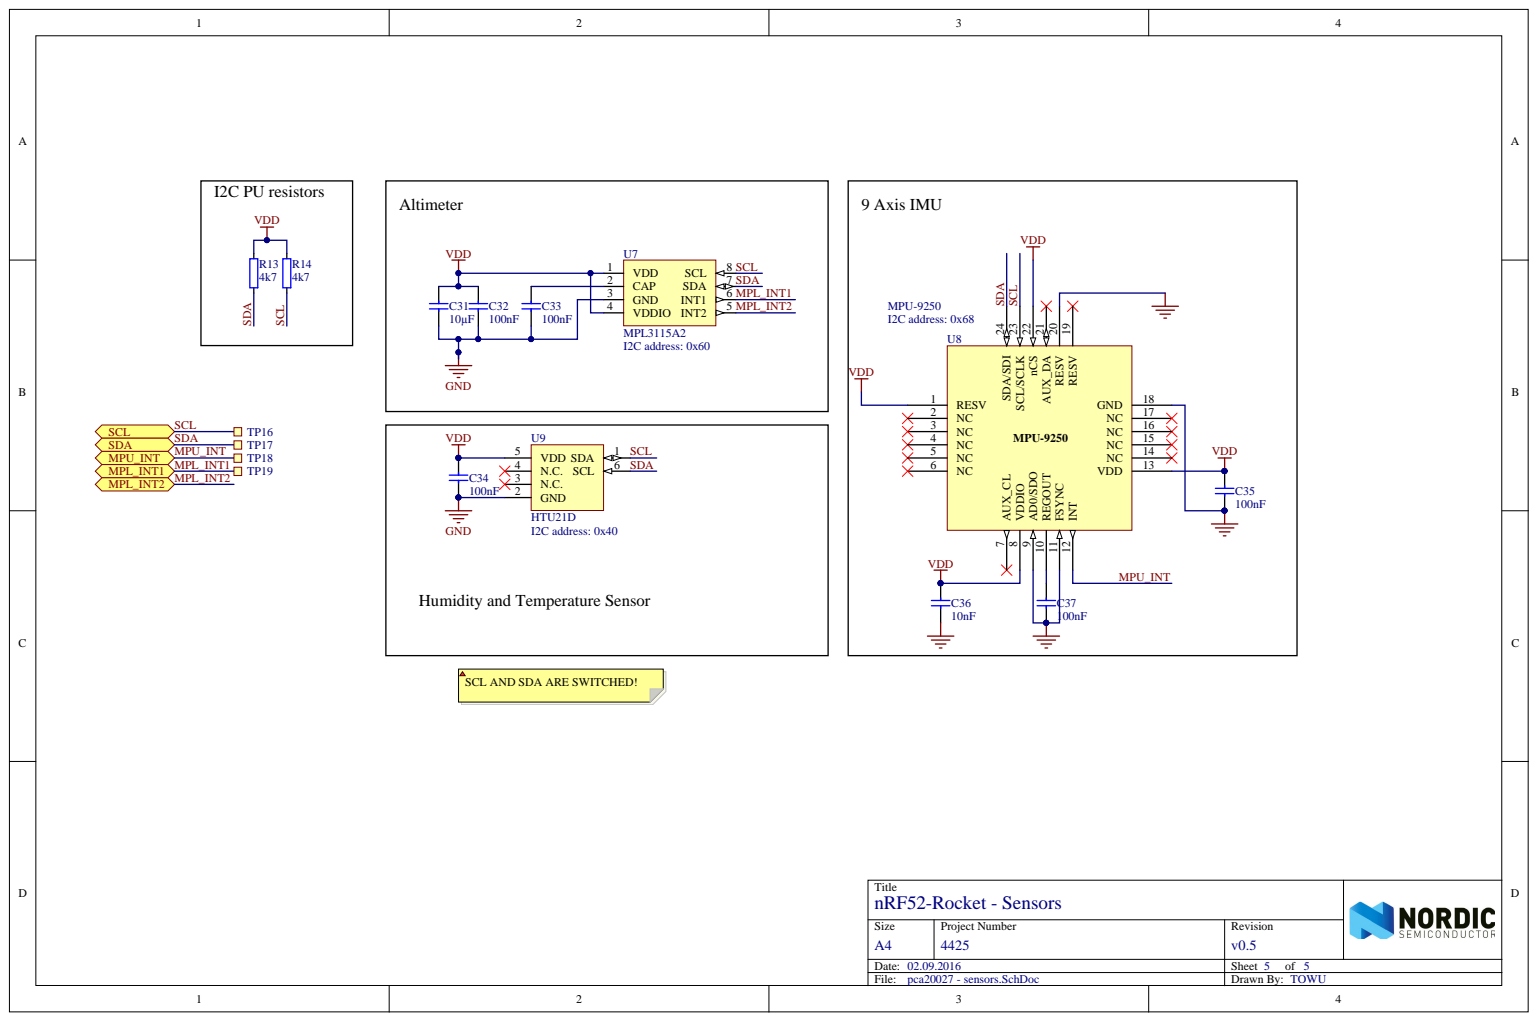
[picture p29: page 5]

SDA/SDI 24 MPU-9250 VDDIO 8

Humidity and Temperature Sensor

SCL AND SDA ARE SWITCHED!

Title nRF52-Rocket - Sensors

Size A4 | Project Number 4425 | Revision v0.5

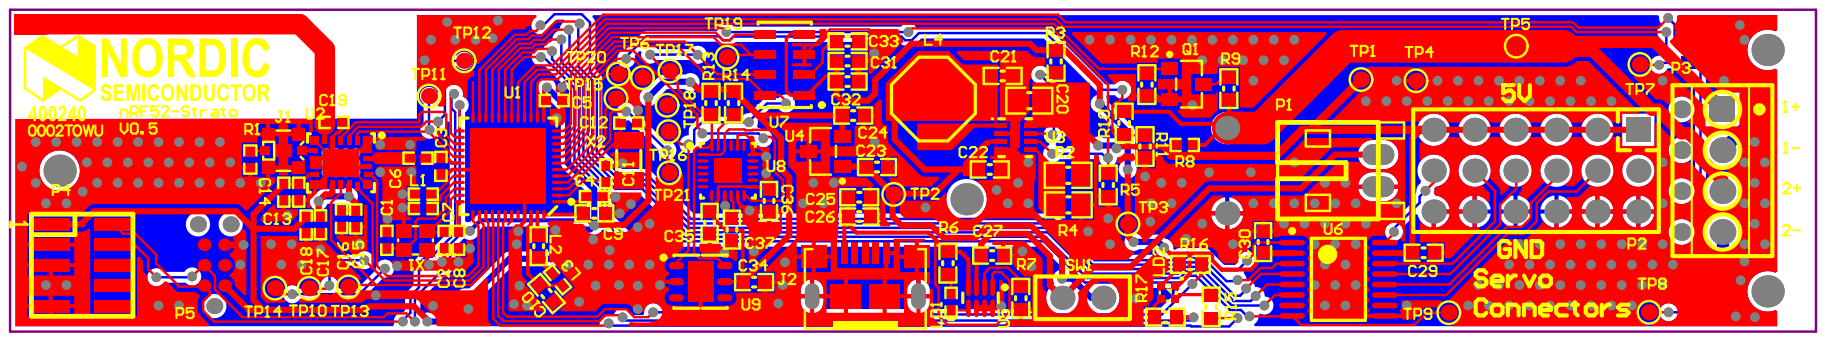
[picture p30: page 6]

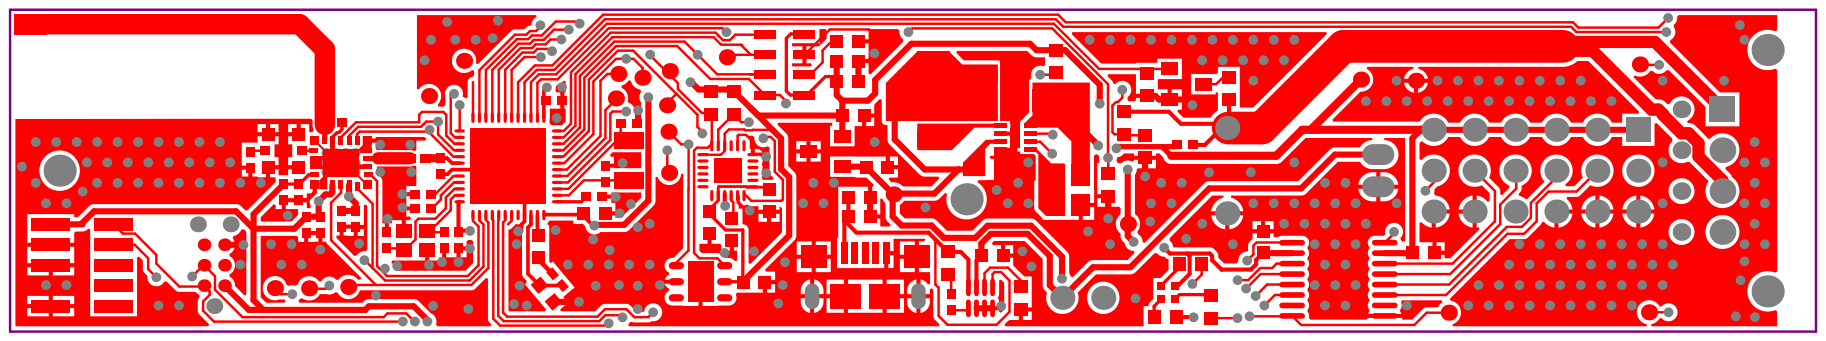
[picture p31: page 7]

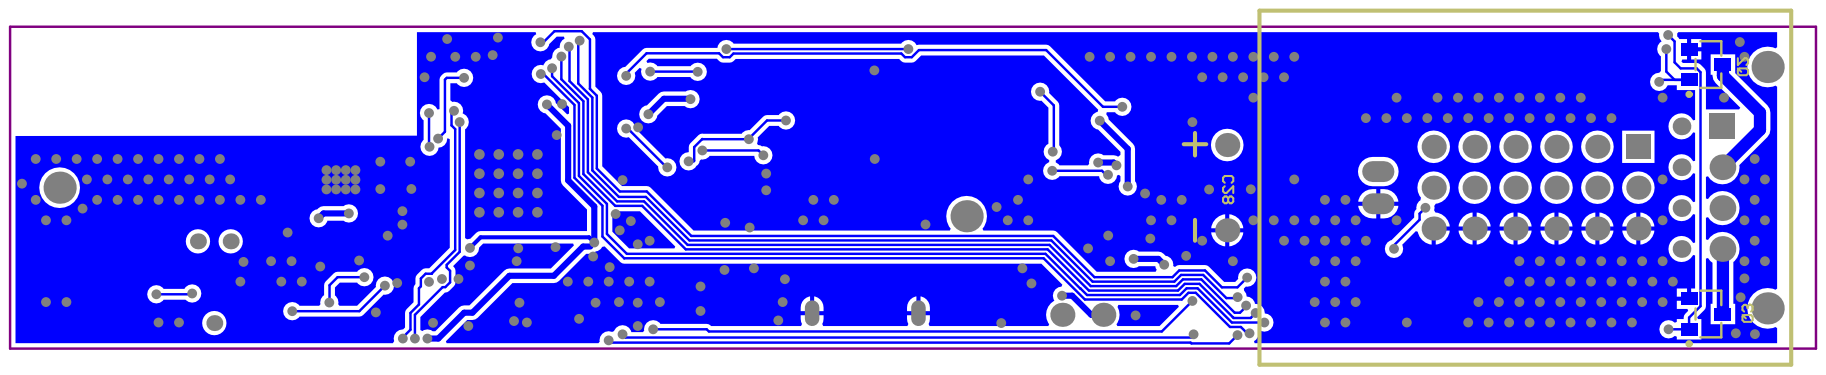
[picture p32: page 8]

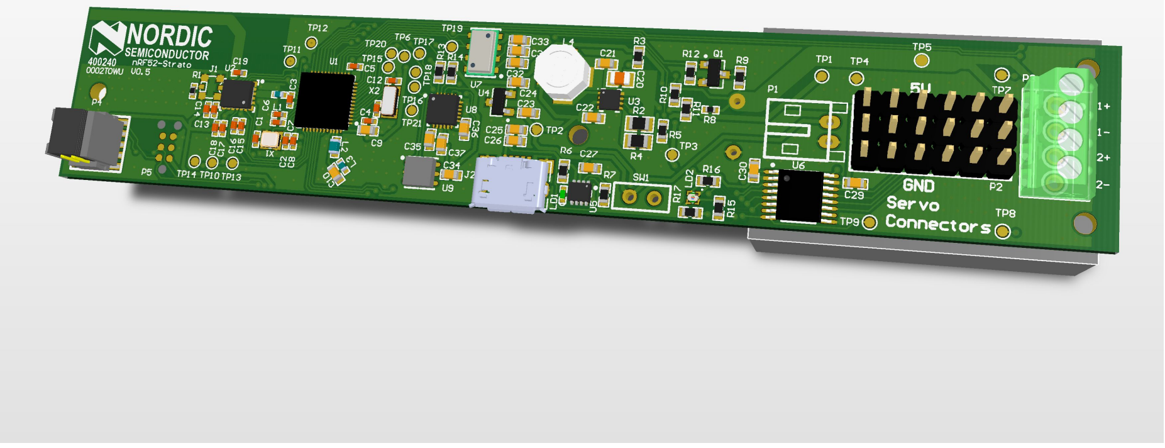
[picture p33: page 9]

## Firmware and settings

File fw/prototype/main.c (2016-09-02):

/* Copyright (c) 2015 Nordic Semiconductor. All Rights Reserved.
 *
 * The information contained herein is property of Nordic Semiconductor ASA.
 * Terms and conditions of usage are described in detail in NORDIC
 * SEMICONDUCTOR STANDARD SOFTWARE LICENSE AGREEMENT.
 *
 * Licensees are granted free, non-transferable use of the information. NO
 * WARRANTY of ANY KIND is provided. This heading must NOT be removed from
 * the file.
 *
 */

/**
 * @brief Blinky Sample Application main file.
 *
 * This file contains the source code for a sample server application using the LED Button service.
 */

#include <stdint.h>
#include <string.h>
#include "nordic_common.h"
// #include "nrf.h"
#include "app_error.h"
#include "softdevice_handler.h"
#include "app_scheduler.h"
#include "app_timer_appsh.h"


#include "strato_app_config.h"
#include "strato_led.h"
#include "strato_ignition.h"
#include "strato_ble_ctrl_sys.h"

#include "pca20027.h"
#include "drv_mpu9250.h"
#include "SEGGER_RTT.h"
#include "app_util_platform.h"
#include "drv_humid_temp.h"

#define DEAD_BEEF                       0xDEADBEEF                                  /**< Value used as error code on stack dump, can be used to identify stack location on stack unwind. */

/**@brief Function for assert macro callback.
 *
 * @details This function will be called in case of an assert in the SoftDevice.
 *
 * @warning This handler is an example only and does not fit a final product. You need to analyze
 *          how your product is supposed to react in case of Assert.
 * @warning On assert from the SoftDevice, the system can only recover on reset.
 *
 * @param[in] line_num    Line number of the failing ASSERT call.
 * @param[in] p_file_name File name of the failing ASSERT call.
 */
void assert_nrf_callback(uint16_t line_num, const uint8_t * p_file_name)
{
    leds_set_rgb(0x00FF0000);
    app_error_handler(DEAD_BEEF, line_num, p_file_name);
}

/**@brief Function for the Power Manager.
 */
#define FPU_EXCEPTION_MASK 0x0000009F
static void power_manage(void)
{
    //Fix FPU stuck in raised flag state
    __set_FPSCR(__get_FPSCR()  & ~(FPU_EXCEPTION_MASK));
    (void) __get_FPSCR();
    NVIC_ClearPendingIRQ(FPU_IRQn);

    uint32_t err_code = sd_app_evt_wait();
    APP_ERROR_CHECK(err_code);
}


/**@brief Function for application main entry.
 */
int main(void)
{
    // Initialize.
    APP_SCHED_INIT(SCHED_MAX_EVENT_DATA_SIZE, SCHED_QUEUE_SIZE);
    APP_TIMER_APPSH_INIT(APP_TIMER_PRESCALER, APP_TIMER_OP_QUEUE_SIZE, true);

    ret_code_t err_code;
    err_code = leds_init();
    APP_ERROR_CHECK(err_code);

    err_code = leds_set_rgb(0x0000FF00);
    APP_ERROR_CHECK(err_code);

    strato_ble_ctrl_sys_init();

    // Enter main loop.

    for (;;)
    {
       app_sched_execute();
       power_manage();
    }
}


/**
 * @}
 */

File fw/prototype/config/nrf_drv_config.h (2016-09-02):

/* Copyright (c) 2015 Nordic Semiconductor. All Rights Reserved.
 *
 * The information contained herein is property of Nordic Semiconductor ASA.
 * Terms and conditions of usage are described in detail in NORDIC
 * SEMICONDUCTOR STANDARD SOFTWARE LICENSE AGREEMENT.
 *
 * Licensees are granted free, non-transferable use of the information. NO
 * WARRANTY of ANY KIND is provided. This heading must NOT be removed from
 * the file.
 *
 */

#ifndef NRF_DRV_CONFIG_H
#define NRF_DRV_CONFIG_H

/**
 * Provide a non-zero value here in applications that need to use several
 * peripherals with the same ID that are sharing certain resources
 * (for example, SPI0 and TWI0). Obviously, such peripherals cannot be used
 * simultaneously. Therefore, this definition allows to initialize the driver
 * for another peripheral from a given group only after the previously used one
 * is uninitialized. Normally, this is not possible, because interrupt handlers
 * are implemented in individual drivers.
 * This functionality requires a more complicated interrupt handling and driver
 * initialization, hence it is not always desirable to use it.
 */
#define PERIPHERAL_RESOURCE_SHARING_ENABLED  0

/* CLOCK */
#define CLOCK_ENABLED 0

#if (CLOCK_ENABLED == 1)
#define CLOCK_CONFIG_XTAL_FREQ          NRF_CLOCK_XTALFREQ_Default
#define CLOCK_CONFIG_LF_SRC             NRF_CLOCK_LFCLK_Xtal
#define CLOCK_CONFIG_IRQ_PRIORITY       APP_IRQ_PRIORITY_LOW
#endif

/* GPIOTE */
#define GPIOTE_ENABLED 1

#if (GPIOTE_ENABLED == 1)
#define GPIOTE_CONFIG_USE_SWI_EGU false
#define GPIOTE_CONFIG_IRQ_PRIORITY APP_IRQ_PRIORITY_LOW
#define GPIOTE_CONFIG_NUM_OF_LOW_POWER_EVENTS 4
#endif

/* TIMER */
#define TIMER0_ENABLED 0

#if (TIMER0_ENABLED == 1)
#define TIMER0_CONFIG_FREQUENCY    NRF_TIMER_FREQ_16MHz
#define TIMER0_CONFIG_MODE         TIMER_MODE_MODE_Timer
#define TIMER0_CONFIG_BIT_WIDTH    TIMER_BITMODE_BITMODE_32Bit
#define TIMER0_CONFIG_IRQ_PRIORITY APP_IRQ_PRIORITY_LOW

#define TIMER0_INSTANCE_INDEX      0
#endif

#define TIMER1_ENABLED 1

#if (TIMER1_ENABLED == 1)
#define TIMER1_CONFIG_FREQUENCY    NRF_TIMER_FREQ_16MHz
#define TIMER1_CONFIG_MODE         TIMER_MODE_MODE_Timer
#define TIMER1_CONFIG_BIT_WIDTH    TIMER_BITMODE_BITMODE_32Bit
#define TIMER1_CONFIG_IRQ_PRIORITY APP_IRQ_PRIORITY_LOW

#define TIMER1_INSTANCE_INDEX      (TIMER0_ENABLED)
#endif

#define TIMER2_ENABLED 0

#if (TIMER2_ENABLED == 1)
#define TIMER2_CONFIG_FREQUENCY    NRF_TIMER_FREQ_16MHz
#define TIMER2_CONFIG_MODE         TIMER_MODE_MODE_Timer
#define TIMER2_CONFIG_BIT_WIDTH    TIMER_BITMODE_BITMODE_16Bit
#define TIMER2_CONFIG_IRQ_PRIORITY APP_IRQ_PRIORITY_LOW

#define TIMER2_INSTANCE_INDEX      (TIMER1_ENABLED+TIMER0_ENABLED)
#endif

#define TIMER3_ENABLED 0

#if (TIMER3_ENABLED == 1)
#define TIMER3_CONFIG_FREQUENCY    NRF_TIMER_FREQ_16MHz
#define TIMER3_CONFIG_MODE         TIMER_MODE_MODE_Timer
#define TIMER3_CONFIG_BIT_WIDTH    TIMER_BITMODE_BITMODE_16Bit
#define TIMER3_CONFIG_IRQ_PRIORITY APP_IRQ_PRIORITY_LOW

#define TIMER3_INSTANCE_INDEX      (TIMER2_ENABLED+TIMER1_ENABLED+TIMER0_ENABLED)
#endif

#define TIMER4_ENABLED 0

#if (TIMER4_ENABLED == 1)
#define TIMER4_CONFIG_FREQUENCY    NRF_TIMER_FREQ_16MHz
#define TIMER4_CONFIG_MODE         TIMER_MODE_MODE_Timer
#define TIMER4_CONFIG_BIT_WIDTH    TIMER_BITMODE_BITMODE_16Bit
#define TIMER4_CONFIG_IRQ_PRIORITY APP_IRQ_PRIORITY_LOW

#define TIMER4_INSTANCE_INDEX      (TIMER3_ENABLED+TIMER2_ENABLED+TIMER1_ENABLED+TIMER0_ENABLED)
#endif


#define TIMER_COUNT (TIMER0_ENABLED + TIMER1_ENABLED + TIMER2_ENABLED + TIMER3_ENABLED + TIMER4_ENABLED)

/* RTC */
#define RTC0_ENABLED 0

#if (RTC0_ENABLED == 1)
#define RTC0_CONFIG_FREQUENCY    32678
#define RTC0_CONFIG_IRQ_PRIORITY APP_IRQ_PRIORITY_LOW
#define RTC0_CONFIG_RELIABLE     false

#define RTC0_INSTANCE_INDEX      0
#endif

#define RTC1_ENABLED 1

#if (RTC1_ENABLED == 1)
#define RTC1_CONFIG_FREQUENCY    32768
#define RTC1_CONFIG_IRQ_PRIORITY APP_IRQ_PRIORITY_LOW
#define RTC1_CONFIG_RELIABLE     false

#define RTC1_INSTANCE_INDEX      (RTC0_ENABLED)
#endif

#define RTC2_ENABLED 0

#if (RTC2_ENABLED == 1)
#define RTC2_CONFIG_FREQUENCY    32768
#define RTC2_CONFIG_IRQ_PRIORITY APP_IRQ_PRIORITY_LOW
#define RTC2_CONFIG_RELIABLE     false

#define RTC2_INSTANCE_INDEX      (RTC0_ENABLED+RTC1_ENABLED)
#endif


#define RTC_COUNT                (RTC0_ENABLED+RTC1_ENABLED+RTC2_ENABLED)

#define NRF_MAXIMUM_LATENCY_US 2000

/* RNG */
#define RNG_ENABLED 0

#if (RNG_ENABLED == 1)
#define RNG_CONFIG_ERROR_CORRECTION true
#define RNG_CONFIG_POOL_SIZE        8
#define RNG_CONFIG_IRQ_PRIORITY     APP_IRQ_PRIORITY_LOW
#endif

/* PWM */

#define PWM0_ENABLED 1
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

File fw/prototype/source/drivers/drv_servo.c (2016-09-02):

#include "drv_servo.h"
#include "nrf_drv_pwm.h"
#include "nrf_drv_clock.h"
#include "pca20027.h"
#include <string.h>

void pwm_event_handler (nrf_drv_pwm_evt_type_t event_type);
void pwm_init(void);
void pwm0_start(void);
void pwm0_update(void);
void pwm1_start(void);
void pwm1_update(void);

//int pwm_scaler = (UINT16_MAX / PWM_TOP );
float pwm_scaler = (65535.0/PWM_TOP);

static nrf_drv_pwm_t m_pwm0 = NRF_DRV_PWM_INSTANCE(0); //Parachute Servo
static nrf_drv_pwm_t m_pwm1 = NRF_DRV_PWM_INSTANCE(1); //Fin Servos

static servo_values_t current_values0;
static servo_values_t current_values1;

static nrf_pwm_values_common_t pwm0_values[] =
    {
        0,/*0,0,0,*/
    };

static nrf_pwm_values_common_t pwm1_values[] =
    {
        0,0,0,0
    };

static  nrf_pwm_sequence_t const pwm0_seq =
    {
        .values.p_common = pwm0_values,
        .length          = NRF_PWM_VALUES_LENGTH(pwm0_values),
        .repeats         = 0,
        .end_delay       = 0
    };

static  nrf_pwm_sequence_t const pwm1_seq =
    {
        .values.p_common = pwm1_values,
        .length          = NRF_PWM_VALUES_LENGTH(pwm1_values),
        .repeats         = 0,
        .end_delay       = 0
    };

void servo_init(void){

    memset(&current_values0,0,sizeof(current_values0));
    memset(&current_values1,0,sizeof(current_values1));

    pwm_init();
    pwm0_start();
    pwm1_start();
}

void servo0_values_update(servo_values_t values){
    // save these values, and update them using the pwm event handler
    current_values0 = values;

    //scale to pwm size
    current_values0.motor1 = current_values0.motor1 / pwm_scaler;
    // current_values1.motor2 = current_values1.motor2 / pwm_scaler;
    // current_values1.motor3 = current_values1.motor3 / pwm_scaler;
    // current_values1.motor4 = current_values1.motor4 / pwm_scaler;

    pwm0_update();
}

void servo1_values_update(servo_values_t values){
    // save these values, and update them using the pwm event handler
    current_values1 = values;

    //scale to pwm size
    current_values1.motor1 = current_values1.motor1 / pwm_scaler;
    current_values1.motor2 = current_values1.motor2 / pwm_scaler;
    current_values1.motor3 = current_values1.motor3 / pwm_scaler;
    current_values1.motor4 = current_values1.motor4 / pwm_scaler;

    pwm1_update();
}

void pwm_init(void){
    uint32_t err_code;
    nrf_drv_pwm_config_t const config0 =
    {
        .output_pins =
        {
            SERVO_1,             // channel 0
            NRF_DRV_PWM_PIN_NOT_USED,
            NRF_DRV_PWM_PIN_NOT_USED,
            NRF_DRV_PWM_PIN_NOT_USED,
        },
        .base_clock = NRF_PWM_CLK_1MHz,
        .count_mode = NRF_PWM_MODE_UP,
        .top_value  = PWM_TOP,
        .load_mode  = NRF_PWM_LOAD_COMMON,
        .step_mode  = NRF_PWM_STEP_AUTO
    };

    nrf_drv_pwm_config_t const config1 =
    {
        .output_pins =
        {
            SERVO_2,           // channel 0
            SERVO_3,           // channel 1
            SERVO_4,           // channel 2
            SERVO_5,           // channel 3
        },
        .base_clock = NRF_PWM_CLK_1MHz,
        .count_mode = NRF_PWM_MODE_UP,
        .top_value  = PWM_TOP,
        .load_mode  = NRF_PWM_LOAD_INDIVIDUAL,
        .step_mode  = NRF_PWM_STEP_AUTO
    };

    err_code = nrf_drv_pwm_init(&m_pwm0, &config0, NULL);
    APP_ERROR_CHECK(err_code);
    err_code = nrf_drv_pwm_init(&m_pwm1, &config1, NULL);
    APP_ERROR_CHECK(err_code);
}

void pwm0_start(void){
    nrf_drv_pwm_simple_playback(&m_pwm0, &pwm0_seq, 1, NRF_DRV_PWM_FLAG_LOOP);
}

void pwm1_start(void){
    nrf_drv_pwm_simple_playback(&m_pwm1, &pwm1_seq, 1, NRF_DRV_PWM_FLAG_LOOP);
}

void pwm0_update(void){

    // | with 0x8000 to invert pwm signal
    uint16_t temp_value = 0;
    temp_value= (uint16_t)current_values0.motor1;
    pwm0_values[0] = temp_value | 0x8000 ;

    pwm0_start();

}

void pwm1_update(void){

    // | with 0x8000 to invert pwm signal
    uint16_t temp_value = 0;
    temp_value= (uint16_t)current_values1.motor1;
    pwm1_values[0] = temp_value | 0x8000 ;
    temp_value= (uint16_t)current_values1.motor2;
    pwm1_values[1] = temp_value | 0x8000 ;
    temp_value= (uint16_t)current_values1.motor3;
    pwm1_values[2] = temp_value | 0x8000 ;
    temp_value= (uint16_t)current_values1.motor4;
    pwm1_values[3] = temp_value | 0x8000 ;

    pwm1_start();

}

// not used
void pwm_event_handler (nrf_drv_pwm_evt_type_t event_type){

    if (event_type == NRF_DRV_PWM_EVT_FINISHED){

    }
}

uint32_t servo0_stop(void){
    uint32_t err_code;
    err_code = nrf_drv_pwm_stop	(&m_pwm0,false);
    return err_code;
}

uint32_t servo1_stop(void){
    uint32_t err_code;
    err_code = nrf_drv_pwm_stop	(&m_pwm1,false);
    return err_code;
}

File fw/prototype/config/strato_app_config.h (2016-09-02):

#ifndef STRATO_APP_CONFIG_H
#define STRATO_APP_CONFIG_H

#include "app_timer.h"

//TIMER CONFIGS
#define APP_TIMER_PRESCALER                             0                                 /**< Value of the RTC1 PRESCALER register. 4095 = 125 ms every tick */
#define APP_TIMER_OP_QUEUE_SIZE                         30                                /**< Size of timer operation queues. */

//SCHEDULER CONFIGS
#define SCHED_MAX_EVENT_DATA_SIZE                       sizeof(app_timer_event_t)
#define SCHED_QUEUE_SIZE                                100

//BLE CONFIGS
#define DEVICE_NAME                                     "Strato"
#define IS_SRVC_CHANGED_CHARACT_PRESENT                 0                                 /**< Include the service changed characteristic. If not enabled, the server's database cannot be changed for the lifetime of the device. */

#define APP_ADV_INTERVAL                                64                                          /**< The advertising interval (in units of 0.625 ms; this value corresponds to 40 ms). */
#define APP_ADV_TIMEOUT_IN_SECONDS                      BLE_GAP_ADV_TIMEOUT_GENERAL_UNLIMITED       /**< The advertising time-out (in units of seconds). When set to 0, we will never time out. */

#define CENTRAL_LINK_COUNT                              0                                 /**<number of central links used by the application. When changing this number remember to adjust the RAM settings*/
#define PERIPHERAL_LINK_COUNT                           1                                 /**<number of peripheral links used by the application. When changing this number remember to adjust the RAM settings*/

#define MIN_CONN_INTERVAL                               MSEC_TO_UNITS(50, UNIT_1_25_MS)             /**< Minimum acceptable connection interval (20 ms), Connection interval uses 1.25 ms units. */
#define MAX_CONN_INTERVAL                               MSEC_TO_UNITS(90, UNIT_1_25_MS)             /**< Maximum acceptable connection interval (75 ms), Connection interval uses 1.25 ms units. */
#define SLAVE_LATENCY                                   0                                           /**< Slave latency. */
#define CONN_SUP_TIMEOUT                                MSEC_TO_UNITS(4000, UNIT_10_MS)             /**< Connection supervisory timeout (4 seconds), Supervision Timeout uses 10 ms units. */
#define FIRST_CONN_PARAMS_UPDATE_DELAY                  APP_TIMER_TICKS(5000, APP_TIMER_PRESCALER)  /**< Time from initiating event (connect or start of notification) to first time sd_ble_gap_conn_param_update is called (5 seconds). */
#define NEXT_CONN_PARAMS_UPDATE_DELAY                   APP_TIMER_TICKS(30000, APP_TIMER_PRESCALER) /**< Time between each call to sd_ble_gap_conn_param_update after the first call (30 seconds). */
#define MAX_CONN_PARAMS_UPDATE_COUNT                    3                                           /**< Number of attempts before giving up the connection parameter negotiation. */

//IGNITION CONFIGS
#define MINIMUM_IGNITION_VOLTAGE                        (3.0f)
#define SUPERCAP_SAMPLE_PERIOD_MS                       (100)

//SENSOR DATA CONFIGS
#define ALTITUDE_SAMPLE_PERIOD_MS                       (150)
#define ALTITUDE_LOG_SIZE                               (400)

//Currently not implemented
#define TEMP_SAMPLE_PERIOD_MS                           (50)
#define ACCEL_SAMPLE_PERIOD_MS                          (50)

//MOTOR CONFIGS
//#define SINGLE_STAGE
#define DOUBLE_STAGE
#define SECOND_STAGE_IGNITION_DELAY_MS                  (2500)

//PARACHUTE CONFIGS
#define D9X2_PARACHUTE_TIMER_DELAY_MS                   (6000)    //Single Stage, one D9 motor on each ignition transistor
#define D9X2_C6X2_PARACHUTE_TIMER_DELAY_MS              (9000)   //Double Stage, 2 D9 motors on one ignition transistor, and 2 C6 Motors on the other


#define CLOSED_DEGREE                                   (45)
#define OPEN_DEGREE                                     (CLOSED_DEGREE+88)
#endif /*STRATO_APP_CONFIG_H*/

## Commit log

2016-07-21 Add pin definitions
2016-07-28 Add PA/LNA driver and broadcasting Also added LED driver
2016-07-29 Add adc functionality and GPIO inits
2016-08-02 Add datasheets and minor uuid fixes
    [amplifier_output_vs_input.xlsx]
2016-08-04 Add BLE interface to 5V power, capacitor dump, and ADC
2016-08-05 Add led current val and ignition ble control
2016-08-05 Add basic servo functions - WIP
2016-08-12 Add parachute servo interface Update weight info and simulation file
    [Mechanical_Info.xlsx]
2016-08-22 Add servo config capability and docs
    [haack-nosecone-200.dxf, haack-nosecone-500.dxf, haack-nosecone.dxf]
2016-08-23 Enable HF XTAL to remove servo jitter
    [strato_ble_ctrl_sys.c]
2016-08-24 Add ground level zeroing of altimeter
2016-08-24 Add Max vertical velocity
2016-08-24 Add failsafe timer for parachute and fin tilt
    [main.c, strato_ble_ctrl_sys.c]
2016-08-24 Add BLE interface to characteristic timer
2016-08-24 Calibrate parachute servo positions
2016-08-25 Recalibrate parachute servo positions
2016-08-28 Retune parachute servo positions
2016-08-30 First Launch
    [Launch Altitude Data.xlsx]
2016-09-02 Minor text fixes
    [Launch Altitude Data.xlsx, Mechanical_Info.xlsx, amplifier_output_vs_input.xlsx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]
2016-09-02 Add scad file for nosecone generation
    [haack.scad]
2017-01-13 Update README and doc files
    [pca20027_bom_documentation.xls]
